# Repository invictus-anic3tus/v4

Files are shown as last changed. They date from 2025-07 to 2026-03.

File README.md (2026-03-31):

<div align="center">
  <h1>v4</h1>
  <p>by anicetus</p>

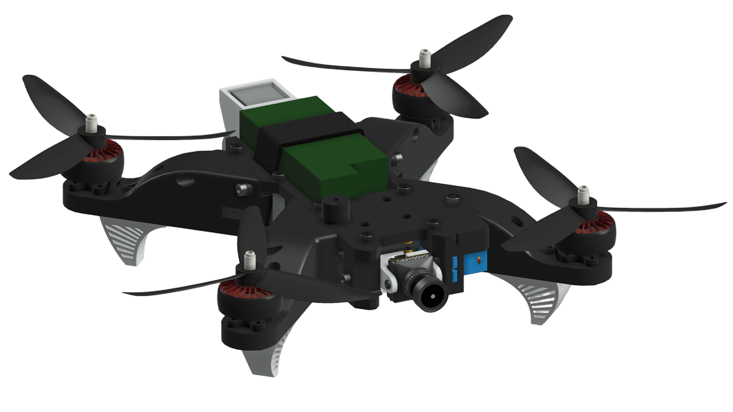
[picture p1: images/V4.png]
Title Image
  

  <p display="inline">
  
  <a href="https://creativecommons.org/licenses/by-nc/4.0/">
    </a> <a href="https://hackclub.com">
    
  </a>

  </p>

  <h1></h1>

  <p>
    A powerful, budget, open source 5" FPV quadcopter frame--perfect for freestyling, casual flying, and even short races!
  </p>
</div>

<sub>This work is licensed under a
[Creative Commons Attribution-NonCommercial 4.0 International License](https://creativecommons.org/licenses/by-nc/4.0/).
</sub>

## Table of Contents

- [About](#about)
- [Features](#features)
- [Specifications](#specifications)
- [Setup](#setup)
  - [Assembly](#assembly)
  - [Firmware](#firmware)
- [Bill of Materials](#bill-of-materials)
- [Contributing](#contributing)

# About

I've been trying to make a drone for a _long_ time. It was my 10th birthday, and my grandparents bought me a toy drone--you know, the kind with the tiny hobby motors and dinky little cameras. I liked flying with it, but it had some drawbacks. For one, it was slow and weak. Flying it in any amount of wind was impossible; it would simply get carried away. It couldn't go fast at all, and speed is really the most fun part of flying a drone. The camera was small and the transmitter slow, so attempting to fly via the mobile camera app was impossible because of the latency. However I will say that it had a 40 min total battery life, between the two 1S 1800mAh batteries it used.

In February of 2024, that all started to change.

It was rough at first. I'd started to get fed up with the silly drone, and I wanted to make one of my own. However, it wasn't _really_ my own at all. I was planning to use the same motors in the old drone, and even the same camera if I was able. (I wasn't.) I thought that by giving it an ESP32 as a brain and an ultrasonic distance sensor as eyes, I could turn the drone into something really neat. The flaw with this idea was that I wasn't really changing anything. Sure, using an ESP32 would let me give it custom programming and stuff, but by trying to use the same motors as the old drone, I was essentially creating a new shell for an old drone.

Besides that, by adding all the extra components, I was making the drone too heavy for the motors to lift. The ESP32s would limit the drone's range (not like it was great to begin with), and all in all it was a fairly silly drone. I blew through three revisions of the thing, each hoping that it would work. Needless to say, none of them did.

It was extremely frustrating. I was more than ready to scrap the entire project and move on to something else.

When Highway came along. [Highway](https://highway.hackclub.com/) is a [Hack Club](https://hackclub.com/)-run You Ship, We Ship (YSWS) event where anybody and everybody who makes a hardware project and journals it along the way gets a grant to build it! From the very start (hehe I got leeks early >:D) I knew I wanted to finish the drone using this program. So I scrapped all my earlier ideas (ESP32 brain, tiny motors) and started the fourth version of my drone! You can read all about my adventure [in the journal](https://github.com/invictus-anic3tus/v4/blob/main/JOURNAL.md).

# Features

- An analog video system, utilizing the Caddx Ratel Pro camera with the HGLRC Zeus Nano 350mW VTX
- 110° rotating camera
- 5-minute flight time per battery
- A Radiomaster RP1 ELRS receiver
- A drone finder buzzer for crashes
- A leading GPS module, the HGLRC M100-5883
- The Speedybee F405 Mini FC-ESC stack
- Powerful iFlight XING E-Pro 2207 2450kV motors
- 5045 propellers
- 3D-printed case
- Only uses M3 screws

## Specifications

| Specification |  Value  |
|---|---|
| Battery Voltage | 14.8V |
| Battery Life | 1550mAh |
| Total Weight | ~650g |
| Weight (Minus Battery) | ~460g |
| Average Total Power Consumption* | 200W |
| Average Flight Time Per Battery* | 6 min |
| Flight Range (Untested) | 400m |

*When flying in normal weather at low to mid-range speeds

# Setup

## 3D Printing Instructions

| Part | Details |
|---|---|
| Main body | 30-50% infill, 6 walls, PETG-CF or similar  |
| Top | 30-50% infill, 6 walls, PETG-CF or similar  |
| Servo casing top | 30-50% infill, Any stiff filament |
| Camera pivot | 30-50% infill, Any stiff filament |
| Legs | 3 walls, TPU or similar |
| GPS mount | 50% infill, TPU or similar |
| ESP32 cover | Any stiff filament |

## ⚠️ PETG-CF Warning ⚠️

The way carbon fiber filaments work is by adding little... you guessed it... fibers of carbon to the plastic to make it more strong and durable. This is great for parts that undergo a lot of stress, such as drones, but the downside is that small fiber shards have all the tendencies of splinters. They can get deep into your skin. They're too small to pick out with tweezers, and only dig deeper when washing your hands. You should wear gloves when assembling PETG-CF parts, and even when transporting the drone. If you do get carbon fibers in your skin, however, try using duct tape to rip them out. Leaving them in can cause permanent itchiness and irritation.

## Assembly

### Camera

First, install an M3 4mm depth brass heatset insert into the large hole on the camera pivot. Next, take the 9g servo and attach the pivot to it. Make sure that the servo is at the 90° position first! Also ensure that the pivot is a tight fit. If the tolerances are too small, the camera could slip and point downwards throughout the entire flight. Note that the camera pivot piece does not have tolerances already. Try printing it multiple times with mulitple tolerances (using the tolerance settings in your 3D printer slicer of choice) to try to find the minimal tolerances you can get while it fits. After attaching the pivot, screw the camera into the slot using the screws it includes. Make sure that it can't wiggle while in the mount. Place the setup in the drone body as seen in the CAD design.

### Body

Assembling the drone body is very easy. First, take the large baseplate piece, and insert M3 brass heatset inserts into every 4.7mm hole, as seen in the CAD design. Next, insert the FC-ESC stack using the M3 screws included with it, with the FC on top! Make sure that the screw heads are at the bottom of the drone. Place spacers on the tops of two diagonally opposite screws, and put the VTX on. Fasten the VTX down with the nuts included with the FC-ESC. Now insert M3 brass heatset inserts into the legs and screw them into the base. Screw in all four motors using the screws they came with, making sure to route the three wires through the tunnels in the base.

Place the battery at the back of the drone, and route a velcro strap through the base to secure it in place. Take the TPU GPS mount and screw it onto the tail of the drone with two M3 screws. Press the GPS into it. Place the ESP32 into its slot, and screw in its panel. Attach the antenna which came with the ESP32 and secure it to the bottom of the drone, using extra tape if needed.

Add a heatset insert to the large hole of the servo top piece. Screw it in place to the main body piece. This is when you'll wire everything. Make sure to route the wires through the top piece for the buzzer before soldering them, since the pins of the buzzer stick through the top piece.

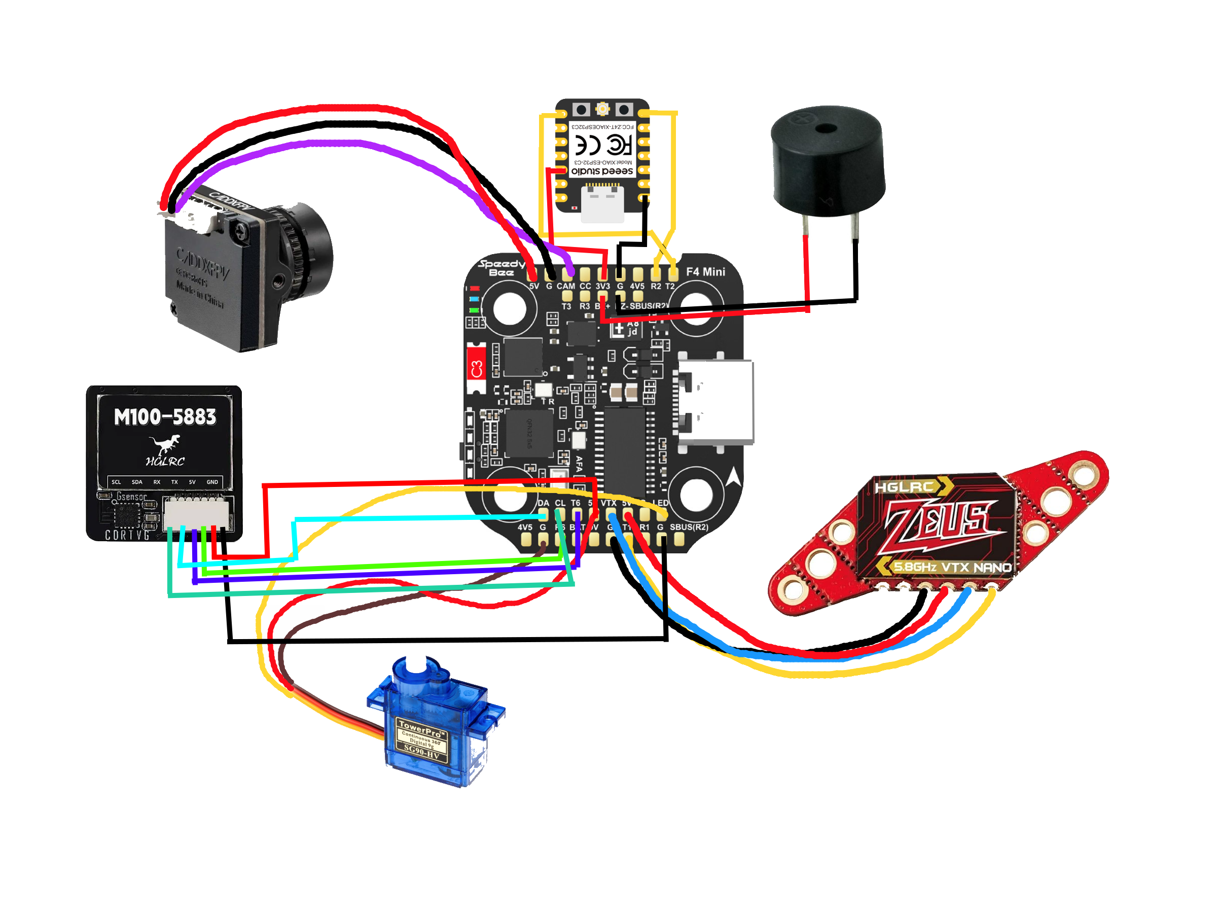
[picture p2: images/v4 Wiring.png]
Main Wiring


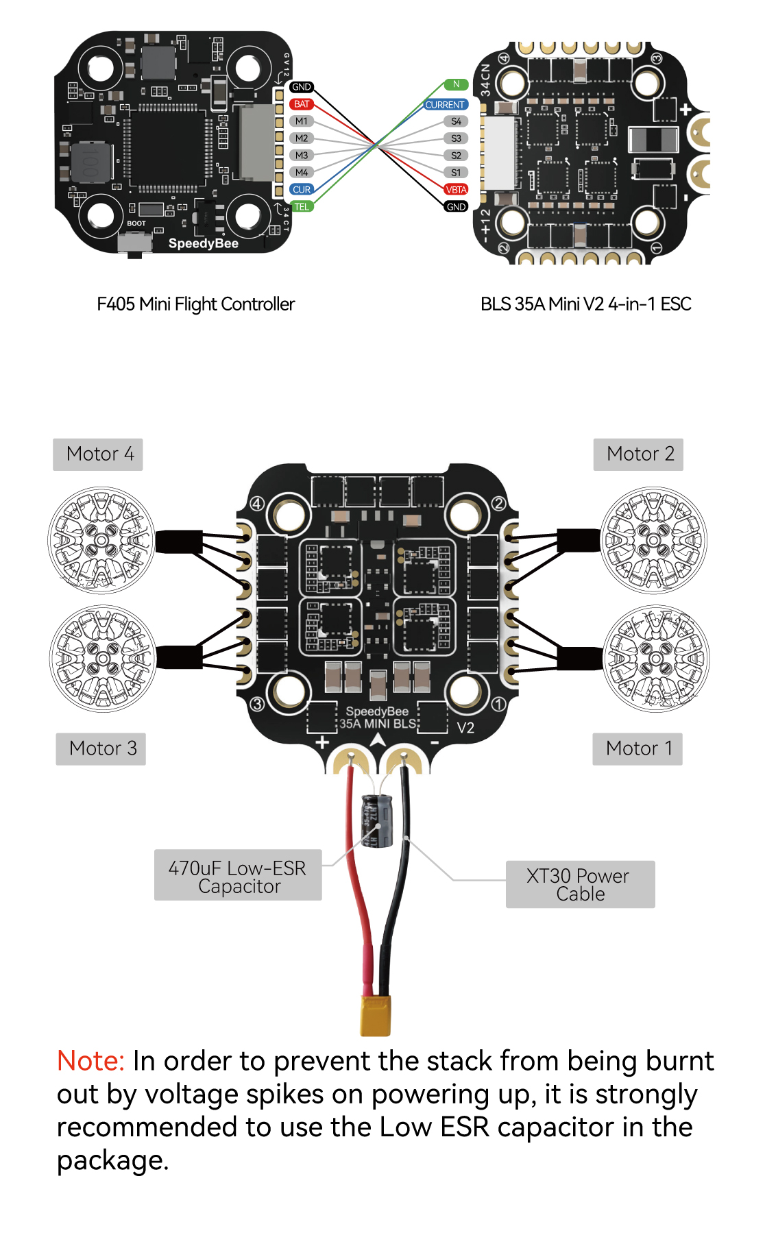
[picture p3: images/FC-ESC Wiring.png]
FC-ESC Wiring


Now add heatset inserts to the top piece. It needs four to secure the FC-ESC stack, as well as eight along the sides to connect to the arms. Screw in the M3 standoffs as shown in the CAD design, and place the top piece on top of them. Screw it to the standoffs and the plastic piece on the front as well as from the arms and to the servo top piece.

All done!

## Firmware

See the [Speedybee F405 Mini manual](https://store-fhxxhuiq8q.mybigcommerce.com/product_images/img_SpeedyBee_F405_Mini_BLS_35A/SpeedyBee-f405-mini-stack-Manual-en.pdf) for firmware and FC-ESC setup.

In Betaflight (or on the SpeedyBee app) make sure that you set the servo limits accordingly. You should watch [this](https://www.youtube.com/watch?v=L-6r2iX1p6s) video to learn how to properly setup the servo. As I haven't done this yet myself, I don't fully know how to do this. The servo has a maximum angle of 30° past midpoint and minimum angle of -80° from midpoint.

# Bill of Materials

|Part |Quantity|Unit Price|Total Price|Amazon Link |AliExpress Link |eBay Link (can change) |Manufacturer |Weight on Drone (g)|Alt. Product |Notes |Cheapest |
|---|---|---|---|---|---|---|---|---|---|---|---|
|analog camera |1 |$31.23 |$31.23 |https://www.amazon.com/Caddx-Ratel-Micro-Camera-Switchable/dp/B0DDBW1D5F/ |https://www.aliexpress.us/item/3256807158842523.html|https://www.ebay.com/itm/157155289889|https://caddxfpv.com/products/ratel-2-1-1-8inch-starlight-sensor-freestyle-fpv-camera |5 | | |amazon, but aliexpress is just a bit more for more reviews|
|FC-ESC Stack |1 |$75.15 |$75.15 |F405 Mini Stack |https://www.aliexpress.us/item/3256806779866237.html|https://www.ebay.com/itm/145520506360|https://www.speedybee.com/speedybee-f405-mini-bls-35a-20x20-stack/ |13.5 | |speedybee f405 mini stack |aliexpress |
|Headset |1 |$54.19 |$54.19 |(none found) |(none found) |(any pre-owned set you can find) |https://emax-usa.com | | |I used the Emax Transporter, feel free to use whatever analog goggles you'd like |manufacturer |
|Buzzer |1 |$2.12 |$2.12 |https://www.amazon.com/Cylewet-Electronic-Magnetic-Continuous-Arduino/dp/B01N7NHSY6/ |https://www.aliexpress.us/item/2255800643239740.html|https://www.ebay.com/itm/324358979243|(none) |2 | |get the 12x9.5 5V kind |aliexpress |
|VTX |1 |$24.99 |$24.99 |https://www.amazon.com/HGLRC-Microphone-Switchable-Transmitter-Betaflight/dp/B08MQ4ZDVF/|Likely not a good seller |https://www.ebay.com/itm/236115710085|https://www.hglrc.com/products/hglrc-zeus-nano-vtx-350mw-for-fpv-racing-drone |2.4 |rush tank ultimate plus - $40 | |amazon |
|drone batteries |1 |$50.63 |$50.63 |https://www.amazon.com/Ovonic-Packs-1550mAh-Battery-Racing/dp/B0821YX6JB/ |$2 cheaper but less buys |4-pack but cheaper per battery |https://us.ovonicshop.com/products/ovonic-100c-14-8v-1550mah-4s1p-xt60-lipo-battery-4pcs|190 | | |ebay (can change) |
|battery straps |1 |$2.67 |$2.67 |https://www.amazon.com/Apex-RC-Products-Non-Slip-Battery/dp/B01MRJ7BUY/ |https://www.aliexpress.us/item/3256806939437749.html|https://www.ebay.com/itm/267163799860|(none) |5 | |Length 250+ mm, width ≤20mm |aliexpress |
|18mm M3 standoffs |2 |$2.30 |$4.60 |(none found) |https://www.aliexpress.us/item/3256808051105851.html|https://www.ebay.com/itm/394867520163|(none) |9 | |M3x18+6, make sure they're threaded, need 6 total |aliexpress |
|Body (filament) |1 |$19.99 |$19.99 | | | | |250 | |any reliable PETG-CF brand is good: Atomic Filament's is the best, but really expensive |amazon (most likely) |
|gps |1 |$18.99 |$18.99 |https://www.amazon.com/HGLRC-M100-5883-GPS-Generation-Compatible/dp/B0CB5N8RQ8 |Very sketchy seller |https://www.ebay.com/itm/365491316265|https://www.hglrc.com/collections/gps-module/products/m100-5883-gps |7.8 | | |aliexpress, but amazon is $0.4 more for better seller |
|Drone battery charger |1 |$24.99 |$24.99 |https://www.amazon.com/SKYRC-B6Neo-Balance-Battery-Discharger/dp/B0CCT2WGNS/ |https://www.aliexpress.us/item/3256805953719537.html|https://www.ebay.com/itm/286231446903|https://www.skyrc.com/b6neo+ | |https://www.amazon.com/gp/product/B0CYBXM3JV/|the skyrc b6 neo is great, but the alt linked amazon one seems good too |amazon |
|Motors |1 |$63.00 |$63.00 |https://www.amazon.com/SPARKHOBBY-Brushless-5-6inch-Propeller-Freestyle/dp/B0D791QQ64/  |https://www.aliexpress.us/item/3256807565015473.html|https://www.ebay.com/itm/364104658026|https://shop.iflight.com/xing-e-pro-2207-2-6s-fpv-nextgen-motor-pro874 |136 | |these are the ones I got, but please please please research your own 2207 models (16x16 mounting pattern)|amazon |
|Props |2 |$2.24 |$4.48 |https://www.amazon.com/PHJKCRWXUL-6x4-5-3-Blade-Propeller-Quadcopter/dp/B0FB7VC2BD |https://www.aliexpress.us/item/3256804148539664.html|https://www.ebay.com/itm/285665860636|(none) |20 | |please research these yourself (but get 5045 size) |aliexpress |
|Heat Set Inserts |1 |$2.50 |$2.50 | | | | | | |buy them from wherever: get M3x4mm size and about 30 count. | |
|Screws |1 |$2.50 |$2.50 | | | | | | |an assorted pack of M3's would be the best, as it needs a bunch of different lengths | |
|Tax | | |$23.48 | | | | | | | | |
|Total | | |$426.80 | | | | |644.7 | | | |

# Contributing

If you'd like to request something, give feedback, or wish to make your own changes, simply open an issue on this repository or email me! (My email is in my profile.)

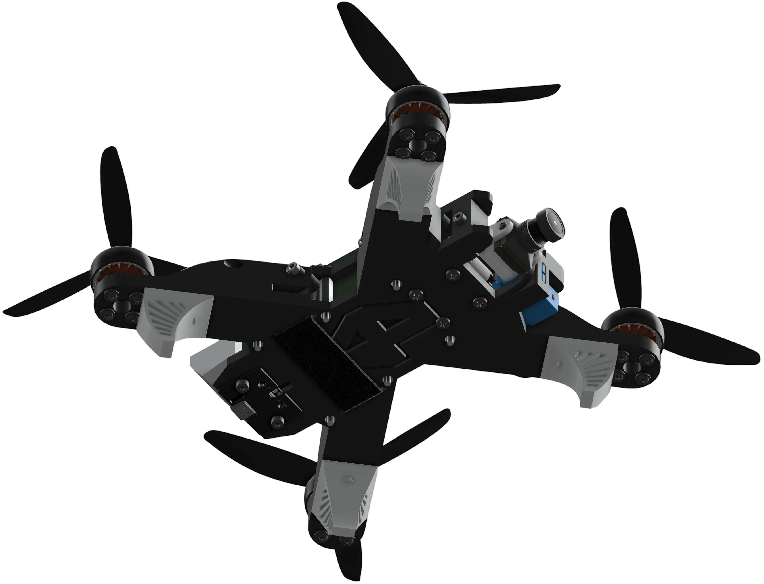
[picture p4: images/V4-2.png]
Ending Image


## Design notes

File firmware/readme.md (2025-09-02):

# How to use firmware

This is the directory containing the files for the controllers and the drone-side receiver. To install the code, first download and install the [Arduino IDE](https://arduino.cc/en/software) app. This will flash the code to your microcontroller. Launch it once installed, and go to File -> Preferences. Add this URL at the end of the "Additional Boards Manager URLs" input: <https://jihulab.com/esp-mirror/espressif/arduino-esp32.git> and hit OK to exit. Go to Tools -> Board -> Boards Manager... and type ESP32. Find the latest version by Espressif Systems and install it. Now to go Tools -> Board -> ESP32 Arduino and scroll down to select XIAO_ESP32C3.

## Uploading to the drone receiver

After completely powering off the drone, plug in the USB port on the back of the drone to your computer, and then open Tools -> Port. If you know which port is your USB for the XIAO, select it. If you're not sure which one it is, close the Port interface, unplug the USB, open it again, and see which one is missing. The one that's now missing is the USB port for the XIAO. Plug the USB back in, and if the port selection doesn't automatically refresh, open and close it and select the correct port.

If unplugging and plugging the USB doesn't make a difference, try using multiple different cables to see if the cable is the issue.

Now you need the SBUS library for the receiver. Open a terminal window and navigate to `C:\Users\{username}\Documents\Arduino\libraries` on Windows, `/Users/{username}/Documents/Arduino/libraries` on Mac, or `/home/{username}/Arduino/libraries` on Linux. Now run `git clone https://github.com/bolderflight/sbus.git`.

Finally, paste the receiver code text from above into the code window in Arduino IDE and hit the forward arrow button in the top left. Once the code is completely uploaded, you can unplug the USB.

## Uploading to the controllers

Now you can plug in the controllers and paste the code in for each one, uploading like before. For the left controller and right controller code files, you'll need to change the MAC address at the top of the code as specified. You can find it by copying the get-mac-address file and uploading it to the ESP32's, then unplugging and re-plugging them back in. See the output in Arduino IDE for the MAC address.

Now replace the placeholder address at the top of the right-controller and left-controller files and upload them like you did with the receiver code. Everything _should_ work now, granted you wired everything correctly!

## Auto-hover

After uploading all the code to their respective ESP32s, you need to tune the hover value. After configuring everything else in firmware, and after you can safely move the drone around a bit, you may notice that when you let go of the left joystick, instead of the drone staying in place, it most likely will either fall or rise slowly. Don't worry--this is normal! Go to the SpeedyBee app and watch the receiver tab while moving the drone up and down. Try to find the point that the drone hovers in place (by moving the left joystick up/down) and note what value (from 1000 to 2000) is displayed for "throttle," the fourth line from the top. Simply subtract 1000 from this number and replace it in the receiver code. Re-upload the code with the updated value. Repeat if you'd like to fine-tune further.

For example, if the drone slowly sinks with the base code, you may find that it steadily hovers at around a value of 1450. Subtract 1000 to get 450, and replace it in the code. But maybe then you see that the drone rises ever so slowly now. Now you can very slowly bring down the left joystick, until maybe you get a value of 1435. Subtract 1000, get 435, add it to the code, and re-upload. Keep doing this until you're satisfied with the drone's hovering.

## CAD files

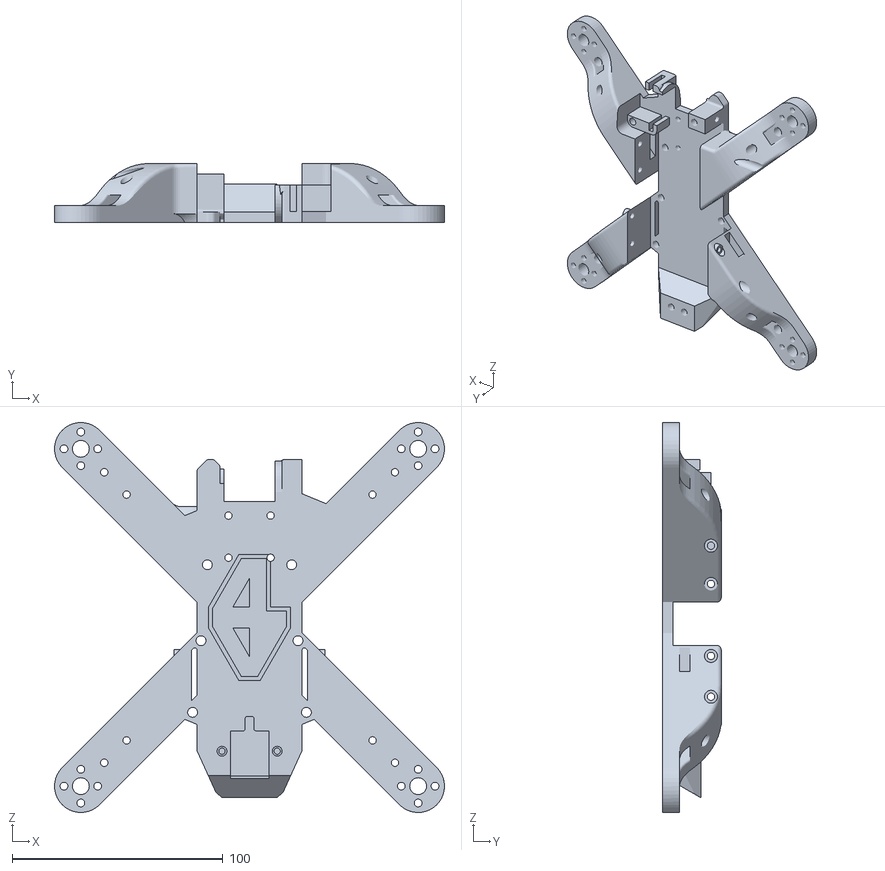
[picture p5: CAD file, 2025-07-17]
cad-and-3d-print/3d-print/Main.stl
185.0 x 28.0 x 185.0

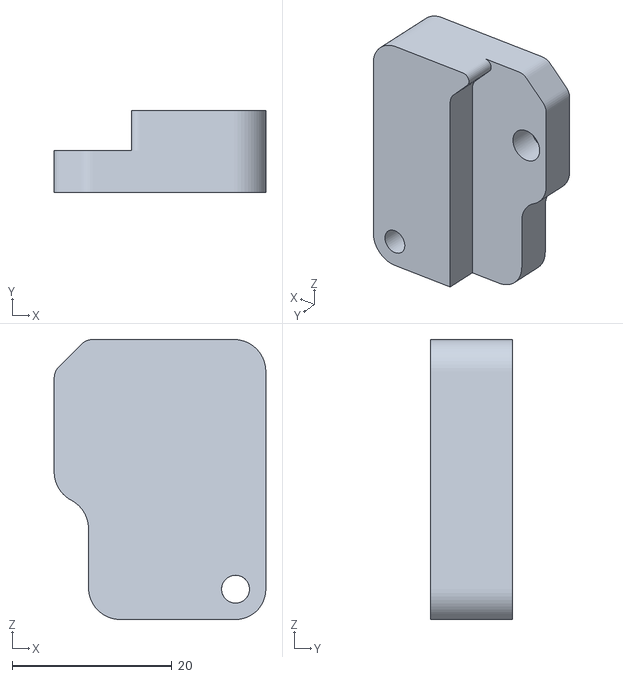
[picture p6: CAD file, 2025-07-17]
cad-and-3d-print/3d-print/Servo Casing Top.stl
26.5 x 10.3 x 35.1

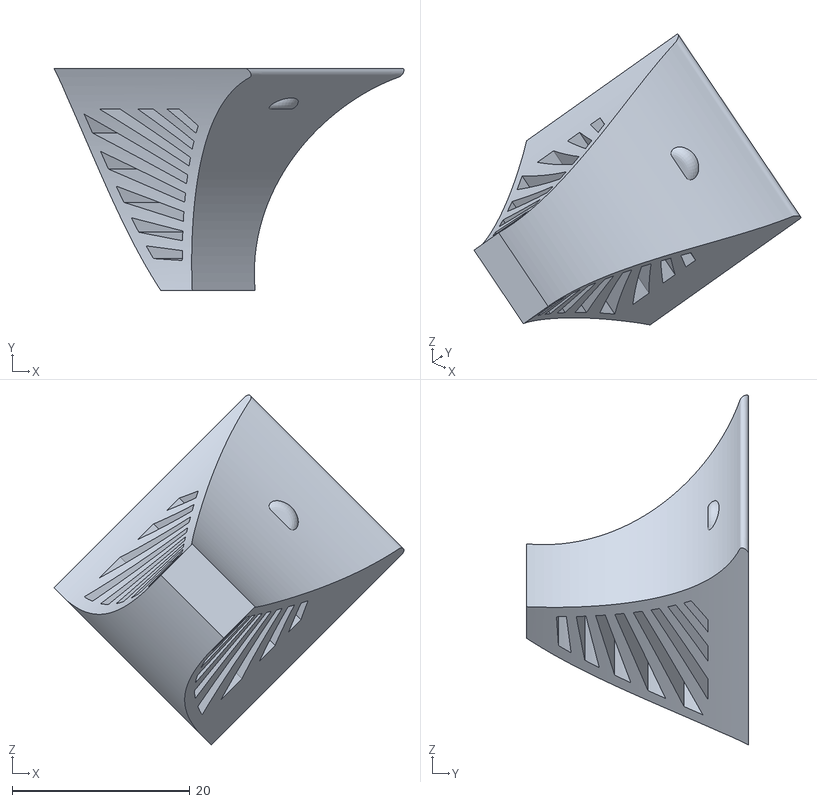
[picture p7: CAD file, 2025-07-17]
cad-and-3d-print/3d-print/Leg - print four.stl
39.4 x 25.0 x 39.4

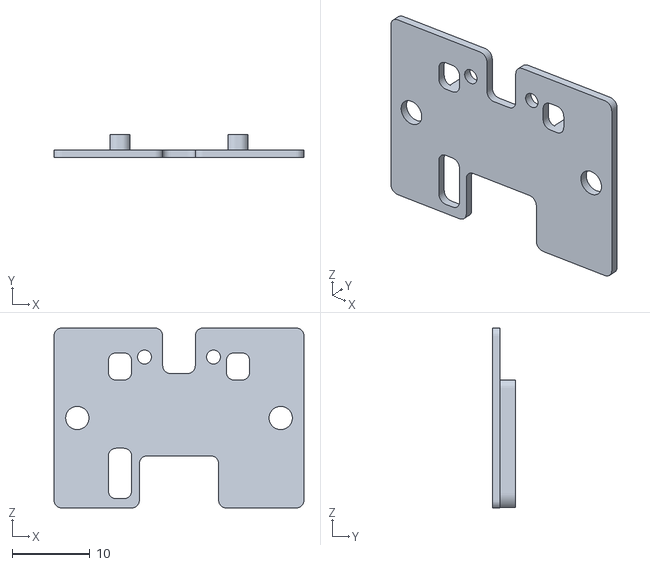
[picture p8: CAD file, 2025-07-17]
cad-and-3d-print/3d-print/ESP32 Casing.stl
32.2 x 3.00 x 23.2

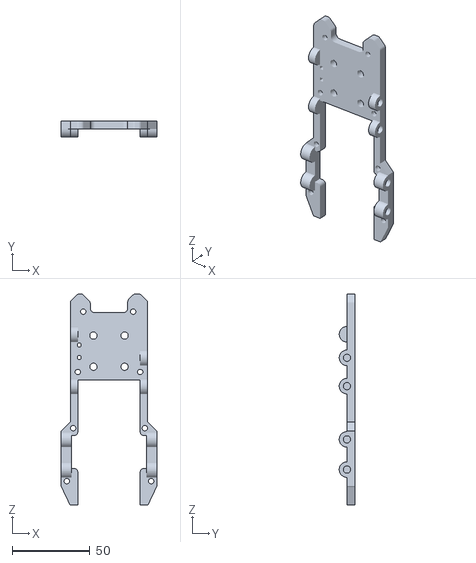
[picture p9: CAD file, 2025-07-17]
cad-and-3d-print/3d-print/Top Piece.stl
61.3 x 9.98 x 135.3

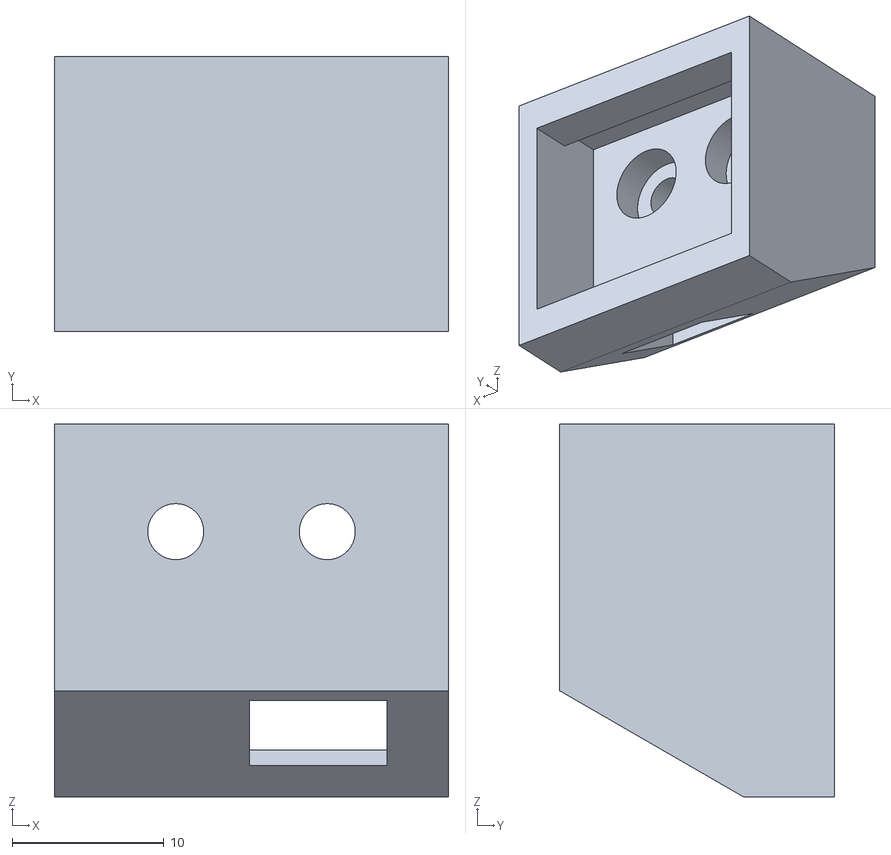
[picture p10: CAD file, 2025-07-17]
cad-and-3d-print/3d-print/GPS Mount - WIP!.stl
26.0 x 18.1 x 24.6

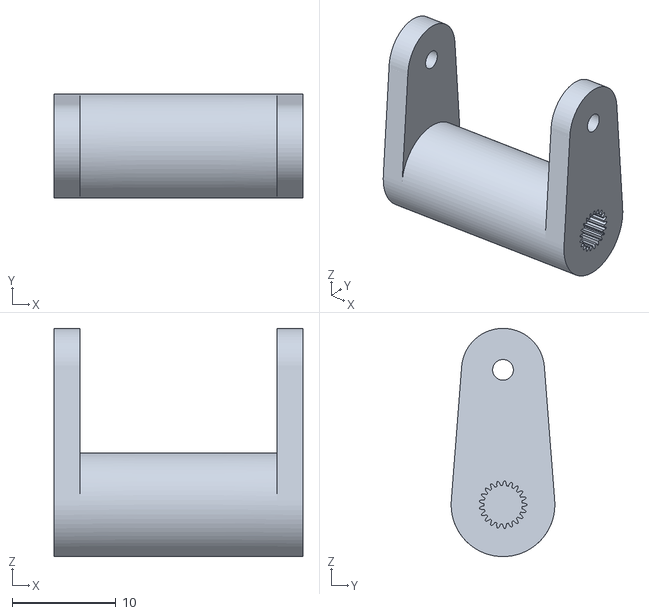
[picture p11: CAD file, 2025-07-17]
cad-and-3d-print/3d-print/Camera Pivot - print with tolerances in slicer!.stl
24.0 x 10.00 x 22.0

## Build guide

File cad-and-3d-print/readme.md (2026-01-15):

# CAD Files

This is the directory where you can find all the CAD files associated with the v4. Keep in mind that all of these files are a work in progress, and haven't been very finely tuned. However, they should still work.

You can find the 3D print files in the 3D Print directory in .stl format. The file name will have instructions as to what filament and basic settings to use, as does the readme in that folder.

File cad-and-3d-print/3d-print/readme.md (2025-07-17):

# 3D Print instructions for the drone parts

| Part | Details |
|---|---|
| Main body | 30-50% infill, 6 walls, PETG-CF or similar  |
| Top | 30-50% infill, 6 walls, PETG-CF or similar  |
| Servo casing top | 30-50% infill, Any stiff filament |
| Camera pivot | 30-50% infill, Any stiff filament |
| Legs | 3 walls, TPU or similar |
| GPS mount | 50% infill, TPU or similar |
| ESP32 cover | Any stiff filament |

Any unspecified values (temperature, etc.) are to the discretion of the maker.

(Please note that as of 7/17/2025 these are untested)

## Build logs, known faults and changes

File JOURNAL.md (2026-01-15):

---
title: "v4"
author: "Anicetus"
description: "My custom FPV drone!"
created_at: "2025-05-27"
---

## total time: 84.5 hrs

# firstly
i want to thank everybody at hack club who's making this possible. if you don't know, hack club is a 100% 501(c)(3) nonprofit run by zach latta + friends made for coders and electronics peoples 18 and under. this project is made possible through their highway to undercity program, where teens are empowered to build their dreams with up to $350 in funding!

so a big thank you out to acon, alex ren, cyao, ducc, bunnyguy, phthallo, paolo, kareem, rhys, kl, ian, tongyu, manitej, cinders, and m0hid!!

## i'm anicetus
if you're reading this on hack club, you may very well already know me. but if you dont, here's a bit of info:  
1. I live in the usa  
2. i'm ok at coding  
3. but i think im pretty good at electronics and stuff!  
4. i've designed a custom keyboard  
5. and a custom 3d printer  

so yeah i've got a bit to put on my resume! but anyways let's get down to business.

# captain's log
yes i stinking know high seas ended in january shut up

## research
### day one - 5/23/25
so today was a long haul of researching tons of different parts. mostly i researched the flight controller and different ways to make it work. i know i have a ton of parts to think about, and idk how im going to get the camera footage from the drone to a rpi for the headset.

anyways lots of progress. i'll give it 2 hrs

### day two - 5/25/25
today i was able to do a ton of research on transmitting video from drone to headset. i learned a bunch about VTX's and VRX's, analog and digital cameras. i posted an essay (lol) in #highway-pitstop asking for opinions and stuff (which I never received by the way,) but it explains a bunch. Here:

so i'd like some opinions on something:
I'm thinking about making an FPV drone plus DIY headset, and I already have the motors and some smaller parts. In the beginning I was planning to make it entirely Raspberry Pi-based, but as I've researched more and more I've uncovered the dire truth: raspberry pi drone == more expensive, more complicated, and less powerful than a standard fpv setup (fc, dedicated drone parts, etc.)

#### (begin post)
The headset is about the same thing: I'd planned to power it with a pi but after researching I've figured out that a simple VRX receiver plus HDMI display could do the job more efficiently. I'm still going to do some sort of DIY controller, probably incorporated into the headset somehow (thinking about handheld joysticks wired to a pi zero in the headset, transmitted with some sort of radio transmitter) but after coming across these hurdles, the project is looking a lot less DIY and more "everybody's already done this, it's nothing new and can't be built on."
My current setup is looking like a pretty normal drone, with a dedicated flight controller and some sort of analog video system. (Digital is way too expensive.) The headset will probably be an HDMI screen paired with a VRX receiver with an HDMI output. I'll either make a standard handheld controller or the split keeb of controllers, with a Raspberry Pi and some sort of radio transmitter (haven't researched this yet.) This is the part I can get really creative with, both with design and with autonomous drone control.
I'd really, really need the whole $350 to pull this off, but here's why I think it's worth it: (I know we don't need approval at the beginning, but similarly to the post above I'd like some opinions.)

1. Researching. I've been researching a bit already, and have been overwhelmed by the varieties and complexities of the most abstruse parts. Most of what I peruse is predominately illegible to me, and every answer just reveals more questions. Also, I can't use AliExpress cuz I hate it.
2. Designing. Creating all the parts will probably be challenging. Drone designs aren't a walk in the park; I know that from my previous few months of trying to make a simple one. This will be the vast majority of the project, as like explained above, drone parts today are largely very plug-and-play.
3. The controller programming. The controller is where I really think my creativity can come into play, and where I can experiment with different functionalities and whatnot. I will likely use a Pi Zero 2 W for it, with simple buttons and joysticks.

Unfortunately, even with my rough BOM, I'm already over the $350. I'll have to do quite a bit more researching and poking around, but if there's anything I've learned with the Anicept Vex, one should never make sacrifices to save money.
Sorry for the essay. Thoughts?
#### (end post)

today i was able to focus harder than yesterday, and got a lot done in ~3hrs

### day three - 5/26/25
today i started composing a rough bom. i researched stuff like batteries, better flight controllers, GPS, etc.

however there was a giant storm and the power went off sooooo

1.5 hrs

p.s. bom at [this link](https://docs.google.com/spreadsheets/d/e/2PACX-1vSraEE6H8Cx8CHQLCQyQCyDCrQoR9ur6-9fPs5dZ3vY1AYaFjepRuHVCa8LgQ7bhq75_Z4WIajNvxX1/pubhtml)

### day four - 5/27/25
today i researched more peripherals, like the buzzer and docking magnets (might not use these) as well as controller parts like the joysticks and buttons. i got a pretty good idea of how I want the joysticks to work:

each controller has an esp32, a buzzer (for power indication), a joystick, two tactile switches, and a small lipo battery
the headset has an esp32 and a rpi zero 2 w
the esp32s on the controllers connect via esp-now (basically a wifi hotspot for esp32 microcontrollers) to the headset, and relay button presses and joystick movement to the headset esp32. that esp32 connects with i2c to the rpi, which processes the data and conveys it to the drone accordingly

i dont really know how im supposed to do this, but ig i'll figure it out :D

today i started teaching my friend javascript :)
2.5 hrs

### day five - 5/28/25
crudcrudcrudcrudcrudcrudcrudcrudcrudcrudcrudcrudcrudcrudcrudcrudcrudcrudcrud

the motors i got in like december or smth are 2450kv cuz i didnt know what it meant and thought well more powerful the better right?

wrong  
so wrong  
really really wrong  
like, kill this project wrong  
because i didnt stop to think "huh more powerful = more power used" and realize that i need a MASSIVE battery to power these motors. thing is, massive batteries cost massive dollars. and this project doesnt have massive dollars. i'd really hate to waste those motors, but idk what else to do. will do more research on this.

2.5 hrs

### day six - 5/29/25
ok i think i figured it out  
so the motors spec page said max amp draw 35A and i was freaking out cuz that's a LOT. but what i didn't realize (but should have) is that the motors wont be drawing 35A 100% of the time... or even 1% of the time. If I can aim for my drone to be 800g or less, including the battery, then I'll only have to use 40%-50% throttle to get it flying well. The spec sheet also says that 50% throttle using 5045 props (what I have) provides 476g thrust at only 100W of power. Four of those are over 1900g of thrust for only 400W of power! That's way plenty for really any drone.

With that in mind, i looked over different sizes of batteries and eventually landed on 4S's, either 1550mAh ($60 for a four pack on eBay) or 2200mAh ($40 for a two pack on amazon.) The 1550's are looking best rn, since it's more for my money.

All that considered, that's around 3 minutes of flight time per 1550mAh battery/4 min for the 2200mAh's, which isn't very good but not as bad as I thought it would be.

Crisis avoided :D

3 hrs

### day seven - 5/30/25
today i spent some time helping other people! it was really gratifying and made me feel good :)  
i didn't do a ton of research tho except for some headset lenses and other smol things. today is the AMA with Strange Parts!!

1 hr

### day eight - 6/2/25
the past few days ive been hanging out with my friend irl so havent got much done. however today i did a bunch of research on cameras and stuff, and found a $55 headset... cheaper than literally just my VRX. makes me wonder if i would be able to just get that instead, seeing as how it does the exact same stuff, better, and cheaper.

2 hrs

### day nine - 6/5/25
ok so yesterday and the day before i was focusing mainly on making a corexy guide writeup thingy so i did basically 0 drone work. however today I think I've got the last little bit of research done! I researched how to get the controller commands to the drone, and I think I've settled on ESP-Now.

For those of you who don't know, ESP-Now is a protocol that transfers data quickly between two ESP32 boards. On each handheld controller is an ESP32, and the right controller will send data to the left. The left combines the received data with its own and sends both to the drone. All ESP32s will be ESP32C3 XIAO boards, preferable due to their external antenna ports rather than the PCB antennae. The ESP32 on the drone receives the data and poops it out of its UART channel, which the FC receives grudgingly.

ESP-Now doesn't have a super great range, but I think that if I can optimize it I'll get good results. I don't need hardly any bandwidth, meaning I can get good range instead. Right now I'm looking at a max of close to 0.2 mi (0.3 km) in good weather and in a fairly open area. I've looked at tests, both using onboard and external antennae, and I've gathered that 500 ft (150 m) is when it begins to drop off a bit. That's pretty good in my opinion, especially since I'm not gonna be flying this thing around the city or whatever.

I also did a bit more headset research. So the headset I was looking at is the Emax Transporter (not 2 lol im not that fancy) headset, and from videos ive seen online it's pretty decent--especially for less than $60 😭 Anyways, I asked if it would be fair if I could get it instead of making my own.

Research for this thing has been actually fairly light. I don't think I'm actually quite done yet, there's always something I forget about.

2.5 hrs

### days ten thru twelve - june 6-12
i've been doing a bunch on the 3d printer and less on the drone from the 6th to the 12th, but for two days I worked on some CAD! I cadded the flight controller when i realized that there wasn't one, and also a few other small things. i found some 3d models online and that's pretty much it. on the 12th i left for church camp! cya soon :D

3 hrs

### day thirteen - june 18
back from church camp! I made a model for the switches im using in the DIY controller, and re-analysed the bom for anything I could get rid of. i popped all the components into one design, and started organizing it and seeing what would go where.

1.5 hrs

### day fourteen - june 20
im multitasking between this and 3d printer so im sorry im doing so little :sob:

anyways i worked on a bunch of cad and started the frame! it's looking quite nice if i do say so myself. I made a lil mount for the GPS at the back. im not super proud of it but i think its ok. does what it's supposed to lol.



2 hrs

### day fifteen - june 22
today I just focused on the drone, and did more frame! I got the servo + camera mounts done, so that the camera can go up and down :D



2 hrs

### day sixteen - june 23
today I fixed a bunch of stuff with the camera mount, and colorized the camera itself, just to make it look nice. I should've done more today, but I got sidetracked by some stuff. However, it's looking quite nice so far!

1.5 hrs

### day seventeen - june 24
today i started the fc-esc stack mount, and i was looking for the included screw sizes. so i opened up my BOM and klicked on my amazon link that i was gonna buy from and... it's out of stock. NOOOOOOO!! It was an amazing price too!!! hopefully it gets back in stock... the ebay link also expired. the aliexpress link is still up, but it's selling for $77, which is a lot more than the amazon one was. I looked around, and the only good ebay links i found were $70 plus shipping. for reference, the original amazon product was $65.99. I looked at the official manufacturer website and was shocked to see it selling for only $60! I put it in the checkout to see what shipping was, and it was free!

You know what wasn't free?

Tariffs.

If you don't know it already about me, I'm politically right and I support President Trump and what he's doing. But $27 tariffs?????? COME ON! It was 45% tariffs. Yep, u heard me right, 45%. That put it at $90. Not ideal.

I'll do more looking around... also cadded the drone legs and made a slot for the esp32 receiver. i edited the gps mount a bit, and positioned it to look nice.

3 hrs

### day eighteen - june 25
today i worked a lot on CAD! i fixed some messed up geometry (drag components aaaahhhhh) and edited the legs to be more flexible and printable. i widened the holes for the battery velcro straps. here's some pics





















2 hrs



### day nineteen - june ??
so I'm writing this on july 3rd, and for the life of me i cant remember what day i actually did this work. i did a ton of work on whichever day it was, and got the top plate probably 75% done! this drone is actually a lot easier than I thought it'd be. Maybe I just got more skilled at CAD since the 3D printer? Idk.

but what I do know is that the end of CAD is actually drawing near. as of writing this, I just bought everything for the printer pi pro, a side-quest I've been taking these past few days. it's a little mod that I'd like to have before continuing work on my 3D printer. more about it on the [github](https://github.com/invictus-anic3tus/Printer-Pi-Pro)!

2.5 hrs

### day twenty - july 3
wow! got a bunch more done today. i connected the two plates via hex standoffs so that they're easy to assemble, sturdy, and not complicated. I colored the components to make them more distinguishable and to make the thing look better. This thing is looking about done!



2 hrs

### day twenty one - july 5
yesterday was the 4th of july (AMERICA DAY!), so i didn't do any work. I got a few responses concerning my design, and I was told that the "wings" which hold the motors were likely to bend and make flying difficult. I started to work on it some, thickening them up. I'm just glad I learned this _before_ assembling!

2 hrs

### day twenty two - july 6
today i pretty much finished the drone body! It's looking really smooth, and the arms are definitely much more sturdy. it looks quite clean, even though it's super bloated (lay off the doritos!) it was a bit complicated getting the geometry to work, but it's way worth it.

Will send pics tmrw.

2 hrs
### day twenty three - july 7
wow! it's already july 7th.... crazy. anyways, I think I've actually finally finished the drone body! I've been working a bunch on the controllers as well. right now, they just look like ugly boxes, but i intend to give them nice curvy shapes and whatnot.

Here's some pics!













3 hrs

### day twenty four - july 8
today was quite productive! I did a ton of work on the controllers and got them half-finished. They're super complex and assembly will be really fun (both sarcastic and not lol).









3 hrs

### day twenty five - july 9
dang I was fire today

finished the controllers! They each have a joystick w/ button for the up/down, forwards/backwards, pitch/yaw, and strafe, as well as two extra buttons on each for more features. The left joystick has a potentiometer for throttle control and camera pitch when a button is pressed. They're kinda ugly and boxy, but for what I had to work with, I'm quite proud of them.









2.3333333333333333333333333333333333333333333333333333333333333333333333333333333333333333333333333333333333333333 hrs

### day twenty six - july 10
today i made some minor changes and did a big ol github overhaul. I researched a bunch on using ESP-Now for the receiver and stuff, and found out it's a bit easier than i thought. i also made a lil hole for the esp32's antenna to route through on the drone. unfortunatley, I realized my drone batteries dont fit, so i need to rework those. also need to add switches for on/off

2.5 hrs

### day twenty seven - july 11
today I did more work on the drone controllers, trying to get the batteries to fit. not a whole lot of time tho because my MOM'S BRITHDAY!!!!!!!!!!!!!!!!!!!!!!!!!!!!!

2 hrs

### day twenty eight - july 13
today i finished the controllers 100% finally! Assembly is definitely going to be a challenge because of how intricate they are, but I'm prepared to make revisions to them if needs be. I also incorporated power switches finally! the most difficult part of assembly is hands down going to be the power wiring. the battery has to go positive to the switch, then to the esp32, and negative straight to the esp32, but all the while, the esp32 will have to be wired to the switches, pot, and joystick. I'm frankly not sure I've allotted enough space for wires to go... I'll see.









Oh poo. I went over my BOM to try to optimize it, you know, review parts that were overkill or unnecessary. I did take out the Caddx Ratel Pro camera in favor of the Ratel 2, which is cheaper and which many claim to be better. That brought the cost down $5, which I was pleased about! I went through, changing stuff and finding cheaper versions on AliExpress, until I got to the VTX. I never inputted the price on it. It's $25. That means that my entire BOM was $25 more than I thought! That brought it to a staggering $373, even after optimizing the other parts. I didn't know what to do, so I just kept optimizing, hoping to be able to find cheaper parts. I was concerned that I might have to get rid of buying carbon fiber filament, which I'd planned on in order to keep the body from flexing. I cut $5 from overpriced joysticks on Amazon, $5 from my battery charger, in favor of a cheaper model, and a cheaper seller of my FC-ESC stack. In the end, I brought it down to $349.93! Ouch.

3 hrs

### day twenty nine - july 15
today i basically cleaned up the BOM some more and started working on the controllers/receiver firmware. I've kinda found an issue though... most drone controllers' throttle control doesn't snap to center, but the joystick modules I'm getting do, and the spring can't be removed without affecting the other direction, which for the the throttle joystick would be yaw. removing the spring would cause the drone to never stop rotating in place! I tried to do a bunch of research on this, but it's hard to figure out what to do. The firmware is a bit more complicated than I'd expected, but I got a bunch done after getting the general idea of it.

3 hrs

### day thirty - july 16
figured out the throttle! I decided to leave it with the spring in... here's how I explained it to ChatGPT when I was brainstorming:

So the "throttle" control is just the percentage of motor power, not distinctly up/down or speed. I had thought that throttle meant motor power while moving, aka speed, and that there was a separate control for up/down that controlled motor power while stationary. However, the former is really just how far I push the forwards/backwards/left/right joystick, while the latter is more of what throttle is.

So the drone is always in either one of two states while flying: no X/Y plane movement or moving in the X or Y direction. If I control throttle in the first state, it simply causes the drone to move upwards the entire time the throttle percentage is above hover, and downwards if the throttle percentage is below hover. If I change throttle in the second state, while the drone is tilted in a direction, it will move faster in that direction but also start to move upwards.

If I leave the spring in, then in the software I can configure the midpoint to be exactly at the hover percentage (likely much lower than 50% in my scenario, somewhere around 25%). This means that in the first state, with no throttle control, the drone will always be at hover. I can specifically control it and pull down to make the drone go down, up to go up, and when releasing, it will hover at that position. In the second state, with no throttle control, the drone will be moving along the X/Y axes at a speed relative to how far I'm pushing the X/Y movement joysticks. When I increase throttle in the second state, the drone will begin to move in the X/Y plane a bit faster, while going upwards as well. The opposite for decreasing throttle. When taking off with the spring, The drone starts up and immediately goes to the hover percentage, meaning it only lifts a small bit above the ground, if at all. If I want the drone not to shake or lift immediately, I can hold the throttle joystick down when arming.

If I somehow take out the spring for throttle but not yaw, in the first state the drone will only be at hover if I specifically set it there, and otherwise will drift up or down. In the second state, the drone will either steadily climb a bit or lower a bit when throttle is the least bit off center, and when deliberately controlling, will stay at that level and continue to rise/fall at that rate until I manually bring it back to center. Taking off would be easier, however, as the motors would be idle until I manually lift the joystick to have the drone rise.

I did a bunch more work on firmware! I am very pleased :3

3.5 hrs

### day thirty one - july 17
today i finalized the repo, i think. i exported all the 3d print and cad files, updated all the readmes for clarity and whatnot, and replaced the CDN-hosted images with locally hosted images. this part was fairly straightforward, but a bit tedious getting all those files.

i'm actually so excited to build and tune this thing... perhaps except for the controllers. those will be difficult. anyways i think code is done and stuff. i also updated the little pot wheel on the left controller to say "camera" instead of throttle. another interesting thing is that amazon is actually sometimes much cheaper than aliexpress, at least for certain parts. It'll be kinda nice getting them overnight and stuff as well.

2.6666666666666666666666666666666666666666666666666666666666666666666666666666666666666666666666666666666666666667 hrs

### day thirty two - july 29
phew! It's been a while! today all the amazon parts finally arrived, after getting the grant and buying everything. I didn't have the time to do any actual work today, so I'll just say 0 hrs. But first, some pics!





Also the GPS and VTX arrived, but I took a video instead of a picture and github doesn't like videos. :b

0 hrs :)

### day thirty three - july 30
today I worked more on the CAD after getting a better idea of what screws I have. I made some adjustments so as not to have to buy any different lengths, and I tested out the PETG CF filament. It's working pretty well! I think tomorrow I'll start printing stuff up... I'm not quite prepared to start a 7 hr print ;b

I'm not going to update the repo cad models quite yet, in case I have to make more adjustments later.

2.5 hrs

### days thirty four thru forty - august 1st thru 7th

by now all the parts have arrived, but I'm still trying to get parts printed. My 3d printer is having a lot of issues, and it's been a struggle trying to crank out this petg-cf. As of the time of writing I have the main drone body going (for the 219734890182nd time) and it seems to be working! I've been doing a bunch of work on the controller models, trying to get them to be easier to assemble. Not a whole lot of progress as a whole but progress nonetheless.

10 hrs

### day forty one - august 15

after 3d printing more and more parts, today I did a build stream in hack club! i got the legs and motors attached, and added heat set inserts to stuff. It's looking quite cool. Installing the motors was surprisingly difficult due to the narrow wire routing tunnels, but I got it in the end.

2.5 hrs



### day forty two - august 16

today i tried to start soldering the battery connector and capacitor to the ESC, but for some reason my soldering iron doesn't agree with that mission. stuff kept going wrong and I had no idea why. Ended today trying to use my solid rosin flux, and it looks like its working a little bit better. whyyyyyyyyyyyyyyyyyyyyyyyyyyyyyyyyyyyyyyyyyyyyyyyyyyyyyyyyy

2 hrs

### day forty three - august 17

YESSSS

today i finally got the battery + capacitor connector attached!!!!!!!!!!!!! :sob: i plugged it in, it powered on, i calibrated accelerometer in betaflight app, took a little look around the gui, and yeah thats pretty much it (at least for now... the day aint over yet)

2.5 hrs

## pretty much big general update - sept 3

what can i say? I've done so much. I stopped logging because it would've been incredibly tedious to recount all of the wires i soldered in a given day and every little thing i've done.

so here's a big fat update. i've finished building the entire drone and controllers and programmed the controllers and drone receiver. the controller communication is working, but for some reason the button presses aren't registering and the fc isn't getting the sbus data. I'll do some more troubleshooting soon.

by this point hours and days are completely out the window... i worked just about every night in the past month on random stuff for it, and there's 0 way to track my hours like that. idk.

## im sorry

its been a long time. like, a really really long time... it's january 15th, 2026, and this drone isn't finished.

the controllers never worked

believe me, i put in a lot of effort into them, but while esp-now worked fine, the receiver never could get sbus to the fc correctly. idk what happened, but i've reached out and have zero clue as to what the issue could be

so i gave up on the controllers

this may be for the better i guess? if i'd followed through with them, i very likely wouldn't have gotten to fly very well. instead, i've spent $80 and got a real controller and a real receiver

sorry again for abandoning the controllers... i've just removed them from the repo.

maybe an update soon when i get the receiver working and the drone in the air, finally.

im so sorry

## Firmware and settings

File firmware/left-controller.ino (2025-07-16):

#include <esp_now.h>
#include <WiFi.h>

// replace with the right controller's MAC address!
uint8_t rightAddress[] = {0xFF, 0xFF, 0xFF, 0xFF, 0xFF, 0xFF};
unsigned long lastSent = 0;
const unsigned long sendInterval = 20; // milliseconds

const int channelNum = 11; // 11 channels total

const int stickXPin = 3; // gpio 3
const int stickYPin = 4; // gpio 4
const int stickButton = 10; // etc.
const int potPin = 2;
const int indexPin = 5; // index finger button
const int middlePin = 6; // middle finger button

// values for the above thingies
int xval = 0;
int yval = 0;
int stickVal = 0;
int potVal = 0;
int indexVal = 0;
int middleVal = 0;

// must match the receiver structure
typedef struct struct_message {
    int source_id; // source A (1) is left controller, B (2) is right controller
    int16_t ch[channelNum];
} struct_message;

// Create a struct_message called sentData
struct_message sentData;

// Create peer interface
esp_now_peer_info_t peerInfo;

// callback when data is sent
void OnDataSent(const uint8_t *mac_addr, esp_now_send_status_t status) {
  Serial.print("\r\nLast Packet Send Status:\t");
  Serial.println(status == ESP_NOW_SEND_SUCCESS ? "Delivery Success" : "Delivery Fail");
}
 
void setup() {
  // initialize serial monitor
  Serial.begin(115200);

  // set device as a wifi station
  WiFi.mode(WIFI_STA);
  esp_wifi_set_protocol(WIFI_IF_STA, WIFI_PROTOCOL_LR);

  // Init ESP-Now
  if (esp_now_init() != ESP_OK) {
    Serial.println("Error initializing ESP-NOW");
    return;
  }
  
  esp_now_register_send_cb(OnDataSent);
  
  // register peer
  memcpy(peerInfo.peer_addr, rightAddress, 6);
  peerInfo.channel = 0;  
  peerInfo.encrypt = false;
  
  // add peer        
  if (esp_now_add_peer(&peerInfo) != ESP_OK){
    Serial.println("Failed to add peer");
    return;
  }

  sentData.source_id = 1;
}
 
void loop() {

  unsigned long now = millis(); // set now to right now

  // if it's been 20ms
  if (now - lastSent >= sendInterval) {

    // read inputs
    // analog vals are from 0 to 4095, but we need to get them to from -1000 to 1000
    xval = map(analogRead(stickXPin), 0, 4095, -1000, 1000);
    yval = map(analogRead(stickYPin), 0, 4095, -1000, 1000);
    stickVal = digitalRead(stickButton);
    potVal = map(analogRead(potPin), 0, 4095, -1000, 1000);
    indexVal = digitalRead(indexPin);
    middleVal = digitalRead(middlePin);
    
    // set values to send
    sentData.ch[0] = 0;         // channel 1  is Y on the right   : Roll (not in this code)
    sentData.ch[1] = 0;         // channel 2  is X on the right   : Pitch (not in this code)
    sentData.ch[2] = yval;      // channel 3  is Y on the left    : Yaw
    sentData.ch[3] = xval;      // channel 4  is X on the left    : Throttle
    sentData.ch[4] = stickVal;  // channel 5  (AUX 1) is left thumb button
    sentData.ch[5] = 0;         // channel 6  (AUX 2) is right thumb button (not in this code)
    sentData.ch[6] = indexVal;  // channel 7  (AUX 3) is left index button
    sentData.ch[7] = 0;         // channel 8  (AUX 4) is right index button (not in this code)
    sentData.ch[8] = middleVal; // channel 9  (AUX 5) is left middle button : buzzer
    sentData.ch[9] = 0;         // channel 10 (AUX 6) is right middle button (not in this code)
    sentData.ch[10] = potVal;   // channel 11 (AUX 7) is the left potentiometer (camera angle)

    // all the values not in this code snippet will be added by the "relay" esp32, on the right controller. the left controller reads its own values and transmits them to the right controller, which adds its values to the mix and sends them to the drone.

    // send message via ESP-Now      address        data                  data length
    esp_err_t result = esp_now_send(rightAddress, (uint8_t *) &sentData, sizeof(sentData));
    
    if (result == ESP_OK) {
      Serial.println("Sent with success"); // yippee!!11!
    }
    else {
      Serial.println("Error sending the data"); // oh noes :(
    }

    lastSent = now; // it was just sent

  }
}

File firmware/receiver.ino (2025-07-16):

#include <WiFi.h>
#include <esp_now.h>
#include "SBUS.h"

/*
  IMPORTANT!
  As soon as you're able to fine-tune hover value, replace the following with that hover value.
  This is in case the controllers fail, so that the drone can lower itself regardless, and also so that the midpoint on the joystick is the hover position.

  You can find it by slowly testing the drone itself while watching the values in the SpeedyBee app receiver tab. They should go from 1000 to 2000. Once you find the hover number in this range, say 1300, simply subtract 1000 to get 300.
*/

const int throttleToHover = 300;

/*
  End important stuff :)
*/

HardwareSerial SerialSbus(1); // UART1
#define SBUS_TX_PIN 21 // sbus pin for communicating with the fc

const int channelNum = 11;

// failsafe variables
unsigned long lastReceiveTime = 0;
const unsigned long FAILSAFE_TIMEOUT = 1000; // 1 second timeout
bool failsafeActive = false;

// non-inverted sbus: if it doesn't register when connected to SBUS (R2), try connected to R3, and vice versa.
SBUS sbus(&SerialSbus, -1, SBUS_TX_PIN, false);

typedef struct struct_message {
  uint8_t source_id;      // source A (1) is left controller, B (2) is right controller
  int16_t ch[channelNum]; // 11 channels, -1000 to 1000 from 2 joysticks with buttons (6 channels), four buttons (4 channels), and a potentiometer (one channel)
} struct_message;

struct_message receivedData;

bool validateData(const struct_message& data) {
  if (data.source_id != 1 && data.source_id != 2) {
    Serial.println("Invalid Source ID");
    return false;
  }

  for (int i=0; i<channelNum; i++) {
    if (data.ch[i] < -1000 || data.ch[i] > 1000) {
      Serial.printf("Channel %d out of range: %d\n", i, data.ch[i]);
      return false;
    }
  }

  int maxCount = 0;
  int minCount = 0;
  for (int i = 0; i < channelNum; i++) {
    if (data.ch[i] == 1000) maxCount++;
    if (data.ch[i] == -1000) minCount++;
  }

  if (maxCount > 8 || minCount > 8) {
    Serial.println("Suspicious data received");
    return false;
  }

  return true;
}


// sbus expects 16 channels, 0-2047 per channel
uint16_t sbusChannels[16] = {0};

// map function: -1000 to 1000 to sbus range 172 to 1811
uint16_t mapToSBUS(int16_t val) {
  if (val < -1000) val = -1000; // these ifs clamp the sbus values in case they're over/under the limits
  if (val > 1000) val = 1000;
  // map to sbus range
  return map(val, -1000, 1000, 172, 1811);
}

void setFailsafe() {
  for (int i = 0; i < channelNum; i++) {
    if (i < 4) sbusChannels[i] = mapToSBUS(0); // set all the joysticks to middle
    if (i >= 4 && i != 10) sbusChannels[i] = mapToSBUS(-1000); // set the aux channels to off
    if (i == 10) sbusChannels[i] = mapToSBUS(0); // servo channel -- set to midpoint of 0
  }

  // fill unused channels (channels 12-16) with middle or default value
  for (int i = channelNum; i < 16; i++) {
    sbusChannels[i] = 992; // sbus midpoint
  }

  sbusChannels[3] = mapToSBUS(throttleToHover-50); // slowly lower the drone
}

// ESP-Now receive callback
//                      mac address,                        data, data length
void onDataRecv(const uint8_t * mac, const uint8_t *incomingData, int len) {

  // Check data length
  if (len != sizeof(receivedData)) {
    Serial.printf("Invalid data length: %d, expected: %d\n", len, sizeof(receivedData));
    return;
  }
  
  struct_message tempData;
  memcpy(&tempData, incomingData, sizeof(tempData)); // copy data from incoming to temp
  
  // Validate the data
  if (!validateData(tempData)) {
    Serial.println("Data validation failed - ignoring");
    return;
  }
  
  // valid data: update receive time and copy data
  lastReceiveTime = millis();
  memcpy(&receivedData, &tempData, sizeof(receivedData));
  
  // Clear failsafe if it was active
  if (failsafeActive) {
    failsafeActive = false;
    Serial.println("Communication restored - failsafe deactivated");
  }

  // map received channels to sbus
  for (int i = 0; i < channelNum; i++) {
    if (i == 3) {
      // make the throttle channel's midpoint at the hover point
      // the left joystick is giving the receiver esp32 values of -1000 to 1000 in the end, where 0 is the midpoint of the joystick
      // this makes sure that 0 is always throttleToHover
      // for example, if throttleToHover is 300, then we're mapping -1000->1000 to 172->428 (two times throttle minus 172)
      // so that the midpoint (receivedData gives a 0, which is when the joystick is at rest) is at exactly throttleToHover
      // this intentionally limits the throttle, as 100% throttle would cause the drone to go incredibly fast, at least for my motors.
      sbusChannels[i] = map(receivedData.ch[i], -1000, 1000, 172, (throttleToHover*2) - 172);
    }
    else {
      sbusChannels[i] = mapToSBUS(receivedData.ch[i]); // map the received data channels (-1000 to 1000) to sbus channels (172 to 1811)
    }
  }

  // fill unused channels (channels 12-16) with middle or default value
  for (int i = channelNum; i < 16; i++) {
    sbusChannels[i] = 992; // sbus midpoint
  }
}

void setup() {
  Serial.begin(115200);

  // wifi and ESP-Now long rage init
  WiFi.mode(WIFI_STA);
  esp_wifi_set_protocol(WIFI_IF_STA, WIFI_PROTOCOL_LR);

  if (esp_now_init() != ESP_OK) {
    Serial.println("Error initializing ESP-NOW");
    return;
  }
  esp_now_register_recv_cb(onDataRecv);

  // sbus init
  sbus.Begin();

  // Initialize failsafe values
  setFailsafe();
  lastReceiveTime = millis();
  
  Serial.println("Receiver initialized - waiting for controller data...");
}

void loop() {

  // if it's been more than one second between controller sends, set the failsafes

  if (millis() - lastReceiveTime > FAILSAFE_TIMEOUT) {
    if (!failsafeActive) {
      failsafeActive = true;
      Serial.println("Communication timeout - FAILSAFE ACTIVATED");
      setFailsafe();
    }
  }

  // send sbus packet every 20ms
  sbus.data(sbusChannels);
  sbus.Write();
  delay(20);
}

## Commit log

2025-07-14 Update README.md - add BOM
2025-07-14 Add v4 BOM.csv
    [v4 BOM.csv]
2025-07-17 Add 3D print files and general CAD files
    [Backing.stl, Camera Pivot - print with tolerances in slicer!.stl, Camera Wheel.stl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]
2025-07-17 Update BOM with screws and heat set inserts
    [v4 BOM.csv]
2025-07-17 Update README.md BOM with screws and inserts
2026-01-15 Remove controllers from repo, update journal
    gave up on the custom controllers :(
    [Backing.stl, Camera Pivot - print with tolerances in slicer!.stl, Camera Wheel.stl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]
